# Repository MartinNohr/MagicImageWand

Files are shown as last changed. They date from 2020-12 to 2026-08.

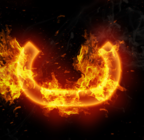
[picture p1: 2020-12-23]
ImageWandSampleImages/144/Fire-Alphabet/C.bmp

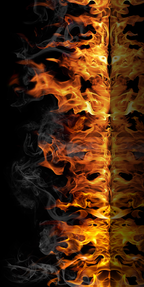
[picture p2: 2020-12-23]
ImageWandSampleImages/144/Fire/FlamesReflection3.bmp

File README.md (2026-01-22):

# MagicImageWand
Similar to the commercial PixelStick or MagiLight products, but designed for DIY.
This is a collaboration project with dirkessl (and possibly others) on a new and improved version of the LED Image Painter project.
It displays bmp files and built-in patterns in the air to be captured with time exposures.
The images are displayed using one or two 144 LED RGB pixel arrays.
The processor was originally the TTGO T-Display with the TFT display, the latest version uses the newer TTGO T-Display S3 chip. Software only support has also been added for the TTGO T4 with the larger display, but no 3D parts have been designed for that board.
It has a nice menu system and single rotary dial button for control.
This device can also be used as a simple light wand with color, saturation, and brightness controls.
It has optional exFat reading to support SD cards >32GB. This is enabled with a switch in the .h file, USE_STANDARD_SD, set to 0. 1 Uses the basic SD library.
<p>For exFat support this library must be included: https://github.com/greiman/SdFat
<br>The display is handled with this library: https://github.com/Bodmer/TFT_eSPI
<p>The file user_setup_select.h needs two lines modified.
<br>uncomment:
<br>#include &ltUser_Setups/Setup25_TTGO_T_Display.h&gt 
<br>comment:
<br>//#include &ltUser_Setup.h&gt

A more detailed setup Instruction for Arduino IDE is available in the Wiki https://github.com/MartinNohr/MagicImageWand/wiki/9.-Compiling-from-source
NOTE: TTGO Magic Image Wand Remote.pdf is used for a remote control camera shutter release designed by dirkessl. It is not part of the MIW project. Support for this concept will be added in the future. It will be possible then to have the MIW actually control the camera shutter.
  NOTE: The JSON library is no longer needed for this project, although it may come back someday! It was used by the bluetooth library for the Phone App. This was deprecated in favor of using a web server.

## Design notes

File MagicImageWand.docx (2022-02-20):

# Magic Image Wand

Using TTGO T1 (T-Display)

# 1 Introduction

## 1.1 History

This design was inspired but not copied from the PixelStick commercial product. I have not owned, used or even touched an official PixelStick, I haven’t even read their manual. I did briefly look at the marketing material on their website to get an idea of how it worked. I was also inspired by the light wand developed by photographer Michael Ross. I started out building one following Michael’s instructions. It used the Mega2560 Arduino and a 2-line display with some buttons. I started adding features and quickly ran out of memory. I also wanted to support a second 1-meter LED strip. At this point I decided to do a total rewrite and use the newer much faster esp32 modules. This let the feature list grow and the additionally the strip display speed was increased dramatically. The first version used an OLED display esp32 from Heltec. After that I discovered the TTGO with a color TFT display. After some more code re-writing and feature adding the TTGO version was created!

## 1.2 Version 2.26

This is the software version used for this documentation.

Changes to 2.26

- Added new scroll mode to the run screen. It now scrolls like the menus. There is a setting in the “Run Screen Settings” to enable the previous method of keeping the top line as the current file.
- Added help explanations for menu items using a long press on btn0. Only a few help texts have been added, more will be added in the future.

## 1.3 Using with Your Camera

Put your camera on a tripod and set it for a long enough time exposure so the shutter is open for at least the time it takes to display the image. Stand at your chosen starting position and open the camera shutter. Press the Image Painter start button and walk from right to left (looking at the camera), or left to right if you prefer, it is adjustable from the menus. Walk smoothly or erratically and hold the wand in the same position or wave it around. Use your creativity and see what kinds of images you can create.

## 1.4 Description

The Magic Image Wand consists of the following major parts. The parts are all connected together into a single unit. The optional second LED strip is easily removed or added so the system fits into a smaller space.

1. LED strip. This is an aluminum extrusion with 144 LEDs and a diffuser cover. The LEDs are available with an adhesive backing that is used to stick the strip inside the extrusion.
2. Fixed Handle. The rotary control button is on the handle which is used to hold the Image Painter. The button is under your thumb and can be pushed and rotated.
3. Rotating Handle. This is useful when two LED strips are attached. It allows the user to spin the light stick.
4. Control Unit. This box holds the ESP32 computer that runs the LED strips and reads the rotary button switch.
  a. TFT Display. The TTGO T1 ESP32 module used includes a small TFT display that is used to show the file selections. It is also used to show menus so that the various settings can be changed. It can even display a preview of the image file.
5. 18650 Batteries. These are the rechargeable batteries that run the control unit and the LED strips. They are held in the case underneath the handle.
6. ARCA tripod mount. This can be placed anywhere on the lower LED strip. It is used for holding the MIW on a tripod which is very useful when using it as a light source. The mount is also used to adjust the balance when using the spinner handle. It can be moved up or down until the balance point is at the spinner handle. This will make rotation much smoother.
7. There are two LED end caps that protect the end of the aluminum extrusions holding the LED strips.
8. Roller Encoder Wheel. This wheel is used to control the display speed while rolling on the ground. It will allow for very exact image timing. The good news is the software supports it but the bad news is that the hardware mount for the wheel has not been designed yet. The connection to this is labelled “frame sensor” on the PCB and schematic.

## 1.5 144 or 288 pixels

The Magic Image Wand uses one or two WS3812B pixel strips that have 144 pixels per meter. Each meter strip is made from two 72-pixel strips. This results in a slight gap in the middle that can be seen in some images. When the second strip is installed the power and data wires make it difficult to get the pixels close together. This results in a dark gap in the middle of the two strips that can be seen with some images. This problem can be avoided by running wires to the ends of the strips instead of the middle. There is an option in the settings to handle this.

The LED count can be set if strips other than 144 are desired.

## 1.6 Limitations

At full brightness, each strip uses 43 Watts when all the LEDs are lit. If full brightness is required then the voltage regulator must be able to supply enough current. However, some images do not have all of the LEDs lit at the same time so the brightness can sometimes be set to full power. For example, if the strip never has more than half of the LEDs on then the power consumption is only 21 Watts. In practice however I have found that due to the long night exposures it is seldom necessary to go brighter than about ¼ power.

## 1.7 Processing BMP Images

The images can be either 144 or 288 pixels in height. They must be rotated 90 degrees CCW and saved as 24bit color in Windows byte order. They can have as many pixels as desired for the width. The easiest way to build an image is to create the image as 144/288 pixels tall and as wide as needed. Remember that black will be transparent in the final image. Once the image looks good it can be rotated 90 degrees CCW and saved as a 24-bit bmp file. The bmp file is then saved to the micro-SD card.

There is a website that will convert images into the correct format.

https://www.essl.de/static/lighty/

# 2 Examples

I have posted some example photos on youtube.com and thingiverse.com. People more creative than me will create much more interesting images. I am including these just to illustrate a few simple examples. You can also go search the web for PixelStick images to get more inspiration.

Here are the links. The youtube links are for earlier versions.

https://www.youtube.com/watch?v=2L3TWKf_4T8

https://www.youtube.com/watch?v=_nibSs949mA

https://www.thingiverse.com/thing:4660045

https://www.thingiverse.com/thing:4613446

https://www.thingiverse.com/thing:4815316 the TTGO version

# 3 Button Operations

All operations can be controlled by the rotary push button on the handle, this makes the image painter usable with one hand. Read about btn0 and btn1 below. The display shows the options and settings and filenames. The dial can be rotated left or right to choose items. The button is clicked to select the current item. A long press is used to access other options and is done by holding the button down for about a ½ second or longer. This long press time is also adjustable if a longer or shorter time is preferred. The system has two modes of operation. After booting the display shows the currently selected file. Rotating the dial left and right will move through the files on the SD card, or the internal patterns if they have been selected. Clicking the button starts the LED strip display. At this point the user walks around with the wand or waves it around depending on what effect is desired. The display shows the progress of the file and how much time is remaining. Settings are available to control the display speed, repeating the file, or even automatically skipping to the next file. The image can even be played twice, first forward and then backward for a mirror like effect. There is a chain option that will play all of the files from the current selection to the final file in the current folder. The brightness of the LEDs are of course also adjustable to balance the lighting with the rest of the scene.

To adjust settings a long press is used on the dial or a simple press on btn1 which will open the last menu that was used. A long press while in the menus returns to the normal play mode. Each menu except the main menu has also at least one entry to return to the previous menu.

## 3.1 Dedicated Buttons – Button0(bn0) and Button1(btn1)

There are two dedicated buttons on the top left of the TTGO device. The top one is called btn0 and the bottom one is called btn1. Both these buttons support both clicking and long presses. A long press of both buttons will reboot the system The functions of these buttons depend on the current operating mode as described next. Common to all modes is that clicking btn1 will always emulate a long press of the dial button.

### 3.1.1 btn0/btn1 During Run Mode

btn0 will preview the current BMP file. This easier than navigating to the menu entry that does the image preview.

Long btn0 rotates the display through all four possible positions. If the display is upside down, the image file will also be rotated upside down. This is useful when using a single strip and holding it high in the air. A long press on the lower button turns on the lightbar feature. These actions can be modified in the system menu.

### 3.1.2 bnt0/btn1 During Menu Mode

btn0 returns to the previous menu. It does nothing if at the top menu. Long btn0 displays some help (if available) about the current menu item.

Long btn1 acts same as clicking the dial button.

### 3.1.3 btn0/btn1 During Integer Entry

btn0 cycles through the allowed increment values. Long btn0 resets the value to the original value. btn1 or dial click saves the new value and closes the number entry.

### 3.1.4 btn0/btn1 During Light Bar

btn0 cycles through the available increment values. Long btn0 increments the delay value which affects the auto cycle mode of the light bar. btn1 or dial click closes the light bar.

### 3.1.5 Btn0/btn1 During Image Preview

Btn0 or btn1 exits preview mode. A long press of btn0 or clicking the dial will show the image information screen. A long press of btn1 toggles the dial rotation mode. The first mode is that the dial scrolls the image preview left and right, this is useful for longer images. The other mode will move through the image files on the SD card. This is used as a visual way to select the current file. Rotating one way previews the next file and the other direction previews the previous file. Folders are ignored. Each long press of btn0 will cycle the starting offset of the image between the values of 0, 5, and 9. This allows the entire 144 pixels to be viewed on the 135 pixel display by changing the start offset.

## 3.2 File Control Settings

There are more details below in the section on menus but here is a quick list of the things that can be changed for controlling the image display.

1. LED brightness.
2. Color Balance. Set the white balance for special effects or to correct color casts.
3. Gamma Correction. Adjust the display to match closer to our color vision at different brightness levels.
4. Column time, how long each frame is displayed. Note that even when set to 0 there is a minimum time which is determined by the amount of time used to load the LED’s. See the menu section below for more details. Frame advance can also be set to manual so the frame only changes when the button is pressed, or the dial is rotated.
5. Fixed display time. It is also possible to have the system calculate the frame hold time. You just set how long in seconds you want the image to take and it will set the correct frame time based on the image size.
6. Reverse. This allows the user to walk from right to left or left to right.
7. Upside Down. This allows the user to hold the wand high in the air without modifying the image file.
8. Pixel Double. This uses two pixels for each one so a 144 pixel images can be displayed on the entire 288 pixels when two strips are installed.
9. Scaling. This will reduce a 288-pixel image to 144 pixels.
10. Mirror. Plays the file twice, first forward, and then in reverse.
11. Chain. Plays all the files from the current file to the last file in the current folder. Files are always in alphabetical order.
12. Start Delay. A wait after pressing the button until the file starts. All delays are specified in 1/10 seconds.
13. Repeat Count. How many times to repeat a file.
14. Repeat Delay. A wait in between file repeats.
15. Chain Repeat. How many times to repeat a chain.
16. Chain Delay. A pause in between chain repeats.
17. Built-In or File. Choose files from the SD or from a set of built-in patterns.
18. Change settings for various built-in patterns.
19. Select Folder. Choose a folder on the SD card to look for BMP files.
20. Display Settings. Control some menu operations and display options.
21. MIW. Manages files that change settings for folders and files. These setting files are loaded when a folder is selected or when a file is run. The settings for a file revert to the original values after running the file. These files are also text and can be edited if desired for special operations. The file version will apply the settings when the named file is displayed. The folder version is loaded when a folder is selected.
22. Saved Settings. Change the settings that can be optionally loaded at boot time. It is also possible to save the current settings and manually load them when needed.
23. Macros. There are ten macro slots (0 to 9) available. Each of these can either load all of the settings or run a recorded sequence of operations. The record command records the images as they are played and the same sequence can then be played again using the run command. The save command stores the current settings which can then be restored with the load command.
24. A dedicated button on the TTGO is used to preview the BMP file on the display.
25. The other dedicated button performs the same operation as a long press on the dial button.
26. Reboot. This will reset the system. It can of course also be done by unplugging the battery from the power supply or including a power switch for the power.

## 3.3 Rotating and Clicking Button

The handle button is rotated and clicked to select different files, menu items, and to change settings. In the menus, boolean values toggle with each click. Multiple selections cycle through all the available options. Integer values go to another screen that shows the minimum and maximum values. Rotating the dial right increases the value while rotating to the left decreases it by the increment amount. The increment amount can be changed by clicking the button which will cycle between different values. One of the values will be a reset to the original value, activated with a long press. A long press is also used to accept the new value and return to the menu. A * indicates the active menu line. A + in front of the menu means another menu will be activated. The “Return…” menu goes back to the previous menu when clicked. A long press will return to file select/run mode. The current menu entry is remembered so that it will return to the same place when the long press is done from the select/run screen.

In select/run mode the current file is displayed on the top line. Optionally the next three files will be displayed below. Rotating the dial right moves the next file to the top line and rotating left moves the previous file back. By default it will stop at the first and the last file. An option allows rollover, so going left from the first file moves to the last file and moving right at the last file will display the first file again. This option also causes menus to behave similarly.

When a file is running after clicking the button the top of the display will show the progress of the file. The current filename is displayed. The line under the file will show the remaining seconds for the file. The rest of the screen will show the various delays, repeats, and chain information when those options are activated.

### 3.3.1 Button Menu Operations

Left/ Right

Select menu

Select file

Inc/ Dec integers

Long press

Open menu system, goes to the remembered menu point

Return to run mode, the current menu point is remembered

Accept integer

Click

Run file when in run mode

Select menu item, including return to previous menu

Toggle booleans

Rotate through multiple selections

# 4 Menus

There are two menu set, full and simple. The full one contains all of the options and can be somewhat time consuming to navigate during normal use. The simple menu has the most used options and is very short.

All menus except the main one have the first line indicating what menu this is. There is a ‘-‘ in front that indicates clicking on this menu will go back to the previous menu. Submenus also have the last entry as “-Back” which will return to the previous menu.

# 5 Simple Menu Details

## 5.1 Menu: Simple

This is a toggle between the full and simple menus. It names the current one in case it isn’t obvious! Just click on it to change to the other one. The setting will be remembered across rebooting.

## 5.2 Images: SD Card BMP | Built-In

This will show which images are currently available, the built-in ones or the SD card BMP files.

## 5.3 Column Time: 10 mS

This displays the current frame time and can be used to adjust the time. It can adjusted from 0 to 500 mS.

## 5.4 Brightness: 30/255

This sets and adjusts the LED strip brightness. 255 is full brightness.

## 5.5 Run Macro: #(0-9)

This will start running the selected macro number, from #0 to #9.

## 5.6 Select Macro: #(0-9)

This command will list all 10 macro names with an indicator if it is available or not. Clicking on one will make that the current macro for the run command.

## 5.7 Sleep

This menu entry makes the MIW enter sleep mode, which uses little power. Pressing any key will wake the system up with the same settings it had before.

# 6 Full Menu Details

Following is a detailed list of all the menu entries and what they do. Menu items that open another menu (a submenu) start with a ‘+’. Most submenus also have a first and last menu entry that returns to the menu above. Depending on the “menu choice” setting found in the menu settings of the system menu, either an ‘*’ is shown in front of the active menu line or the menu line is highlighted. The top menu will have a small white triangle indicating that there are menu items that are not visible due to scrolling. Just keep rotating the knob to the left and they will appear. Similarly the last entry on the screen will have a small white triangle if there are more menu items below. Scroll right to make them visible as the ‘*’ or highlight indicator moves down.

The submenu details are also described below after each menu item. Submenus have a ‘+’ at the start.

Some menu items may change depending on other selections. For example, chain options are not displayed unless chaining is enabled.

## 6.1 Menu: Full

Select this to toggle between the simple and full menu systems.

## 6.2 Images: SD Card BMP | Built-In

Clicking this selection will toggle between running files from the SD card or using the built-in patterns.

## 6.3 Preview BMP

This will display the currently selected BMP file on the screen. Note that the upper dedicated button (button 0) does the same operation. This menu item appears only when CD Card is selected. Since the images are 144 pixels and the display is only 135, 9 pixels total are trimmed from top and bottom of the image. The starting offset in the preview menu sets how many pixels are ignored at the top. Long press btn0 can be used to change this value while previewing. Each long press of btn0 cycles through the values of 0, 5, and 9 pixels. The image can be scrolled left and right using the dial if the image is longer than 240 columns. The sideways scroll amount defaults to 120 pixels, but the amount can be set in the system menu display settings menu A single click toggles between the image preview and a screen showing the width and height of the image. Pressing the upper preview button, or a long press on the dial, or the lower dedicated button exits the preview display.

The image preview has two modes for using the rotating dial. The default mode is to scroll the iamge sideways when possible. The other mode will scroll through the image files. This is a visual way to select the current file. The modes are toggled by a long press of btn1.

Clicking the dial button while previewing a file will display a screen with the size of the image in pixels, the length that should be walked for the correct aspect ratio, and how long the image will be displayed at the current column hold time.

There is a dedicated button on the top left that can also be used to preview the file. Pressing it again will return to the previous menu or file selection.

If the images are designed for the second LED strip then the images can be 288 pixels high. The preview function will then ignore every other pixel so the preview will fit in the display.

The preview can also be set to automatically scroll if it is long enough. The speed and amount of pixels to jump in this auto scroll mode are adjustable from the preview settings menu found in the system menu.

## 6.4 +Image Settings

This submenu has the settings that control display attributes of the image files. The frame hold time is also used by some of the built-in image functions.

### 6.4.1 Timing Type: Column | Image

This is a Boolean that switches between using a set frame hold time for each column of the image file or a calculated time based on the desired total display time. It is sometimes more convenient to set the total time that the image file is displayed. This mode will automatically calculate the frame hold time such that the image will display for the chosen time. It is possible to request a time that is too fast for the image painter. If the calculated frame hold is less than about 4 mS the software cannot read the SD card fast enough to keep up. The image painter will do the best it can, and the actual time will be displayed on the screen as the image plays.

### 6.4.2 Column Time: 10mS

This selection shows and allows to be changed, the time in mSecs (see note below) that each line of information from the BMP file is displayed on the LED strip. It is commonly used to adjust the walking time while the file is being displayed. It is only applicable when Frame Advance is set to auto. The valid range is 0 to 500 mS.

Note: This time is actually added to the minimum time that it takes to update the LED’s in the strip. Each bit of information takes 1.2 uS and each LED needs 24 bits. If there are 144 LED’s then the total time to load the data is 1.2 uS x 24 x 144 = 4.32 mS. There is also a reset time at the end that loads the data into the LED’s of >50 uS. Some brands require up to 1 mS so it is safest to assume that the column update time is about 5 mS. This time is added to the time set in the frame hold value, I.E. a hold value of 0 will still have a 5 mS frame time. There might also be additional time required for reading slower SD cards. Also be aware that displaying the file in reverse will slow down due to reading the SD file in the reverse order. A 900 column image would in theory take about 3.9 S. In testing we have found that reading the SD card actually slows this down to about 6 Seconds. Work is being done to try and improve this.

### 6.4.3 Image Time: 5 S

When image time is selected as described above in Column Time this menu item allows the time to be set in seconds that the image will be displayed. The necessary column time will be calculated and used while displaying the image file. This value will not be saved in the column time so if column time is selected again it will show the original value.

### 6.4.4 Start Delay: 0.0 S

This value delays the image display after the start button is pressed. It can be set in 1/10 second increments.

### 6.4.5 Fade I/O Columns: 0

This value is the number of columns (aka frames) that will be used for fading in and out during the display of an image file. It does not apply to the built-in patterns. For example, setting it to 20 will mean that the first 20 frames will start at a brightness of 0 and increase to the specified LED brightness. The last 20 frames will fade down to 0 on the last frame. This gives a softness to the starting and ending sides of the image. An option to have separate values for starting and ending has been considered but has not been implemented yet.

### 6.4.6 Upside Down: Yes | No

When set, the image pixels will be reversed. This allows the LED bar to be held upside down without making the image upside down. Note that a long press on button 0 will also toggle this.

### 6.4.7 Running Dial: None | Brightness | Speed

This menu controls what the dial does during image display. The brightness or speed (column display time) can be changed during display by rotating the dial. This can be used to create more interesting image effects by rotating the dial while walking.

### 6.4.8 Walk: Right-Left | Left-Right

This option changes the direction that the file is read for display. This allows the image to play forward or reverse. This allows the user to walk in the other direction or to simply reverse the image from left to right. The default is right to left, looking back at the camera. Right to left is usually best when recording a sequence of images into a macro. The images will then play back in the same order. If left to right is chosen, then the images recorded will play back in the reverse order. This is particularly important when spelling words with the individual letter image files during macro recording.

### 6.4.9 Play Mirror Image: No | Yes

This plays the image twice, once forward and then in reverse. This creates a mirror like effect.

### 6.4.10 Mirror Delay: 0.0 S

This is the delay before starting the mirror image display after the normal display is finished. I is used to create black space between the two parts of the image.

### 6.4.11 Scale Height to Fit: No | Yes

If the image is taller than 144/288 this option will ignore some pixels so that only 144/288 are displayed. It does not do any fancy scaling like Photoshop by looking at adjacent pixels, it simply ignores half of them so the image will fit.

### 6.4.12 144 to 288 Pixels: No | Yes (only when 288 pixels is set)

This doubles every pixel so a 144-pixel image will fill all 288 pixels. Of course, there isn’t any increase in resolution, but it does fill two strips if you don’t have a 288-pixel image.

### 6.4.13 Frame Advance: Auto | Step

In auto mode the frame hold time is used. In step mode each line is displayed until the button is pressed, the dial is rotated, or the frame (aka wheel) pulse counter closes the contact. If the frame pulse counter is zero then the dial is used to advance frames. Rotating to the right or clicking will display the next frame from the file. Rotating to the left will display the previous frame. This enables some creative uses of image by rotating the wheel left and right. Note that the mechanical wheel pulse counter has not been designed yet.

### 6.4.14 Frame Counter: 0

This value is the number of wheel pulses that will advance to the next frame when manual frame advance is set. Note that this option is set to a non-zero number it disables using the rotary dial to advance frames.

## 6.5 +Repeat/Chain Settings

This submenu contains settings that are used to repeat and chain images. Except for the chaining option it also applies to built-in images.

### 6.5.1 Repeat Count: 1

This is the number of times to repeat an image.

### 6.5.2 Repeat Delay: 0.0

When repeat count is greater than one this value will cause a delay before the image starts again. It is set in 1/10’s seconds.

### 6.5.3 Chain Files: Off | On

When this option is on all the files from the current one to the end of the last file in the current folder will be displayed. Since filenames are always sorted alphabetically this option will show a sorted list of files. If some other order is desired it is also possible to use the macro command to record the file order for display.

### 6.5.4 Chain Repeats: 1 (only when chain files on)

The entire chain will be repeated this many times.

### 6.5.5 Chain Delay: 0.0 (only when chain files on)

This time value is applied before starting each chain repeat after the first one.

### 6.5.6 Chain Wait Key: No | Yes (only when chain files on)

This is a Boolean setting that when true will wait for a key click or rotation after each file is displayed. You can then decide when to start showing the next file in the chain.

## 6.6 +LED Strip Settings

This submenu has settings for the LED strip.

### 6.6.1 Max Brightness: 25/255

This is the brightness from 1 to 255. Values above about 45 should not be used with the light bar unless the power supply can supply sufficient current. 255 white will use almost 7 amps! The version of the PCB with the onboard power supply can only supply 1.5A continuous. More than that will cause overheating and eventual destruction. High brightness values can be used for shorter image displays of course if there is some cool down time. A minute is usually sufficient for this. In practice it has been found that a brightness level of 15 to 25 is more than adequate for night photography. 7A would likely only be needed in a light bar used for studio lighting.

### 6.6.2 LED Controllers: 1 | 2

This is set to “1” or “2” depending on whether you have the second strip installed. There is not any method to detect a strip connected to the second control lines so it must be manually selected. When this value is changed a reboot is necessary because the fastled LED library does not handle runtime changes very well.

### 6.6.3 Total LEDs: 144 | (up to maximum value) 512

This is a number specifying how many total LED’s are available. It can be set from 1 to 512. For example, if there are two 144 LED strips, then this should be set to 288.

### 6.6.4 LED Wiring Mode: Middle | Serial | Outside

This option allows the wiring to the LED strips to be arranged in different ways to optimize the wand. Putting both LED inputs in the middle of the wand means shorter wires that do not have to extend to each end of the wand, but there will be a larger gap in the middle between the two strips since it is difficult to get the LED strips close with the power connecters there. Putting the bottom strip input on the bottom and connecting the output of the bottom to the input of the top LED allows for only one control wire but there will still be a black stripe in the middle due to the spacing needed for the wires. This is same problem as the first wiring situation. If the top strip has the data input at the top, then the gap in the middle can be eliminated. Make sure no electrical contact happens in the middle between the two LED strips. This approach does mean that it is necessary to run wires out to both ends of the wand, but in return there is no black stripe in the middle when using the wand.

- Middle - Both strips have data input in the middle.
- Serial - Bottom strip is fed data from the bottom and the middle has a connection through to the upper strip. This uses a single contoller while the others can use one or two controllers.
- Outside - The top strip is reversed and there is no connection between the strips in the middle. Both strips require long wires to the outer data feed locations.

### 6.6.5 Gamma Correction: On | Off

This option modifies the displayed colors at different brightness levels to more closely match our eyes color perception.

### 6.6.6 White Balance R: 255

This manually sets the strip Red brightness Values range from 0 to 255.

### 6.6.7 White Balance G: 255

This manually sets the strip Green brightness.

### 6.6.8 White Balance B: 255

This manually sets the strip Blue brightness.

### 6.6.9 Show White Balance

Selecting this displays the before and after result of setting the RGB levels. It runs for about 5 seconds.

## 6.7 +Various Built-In Settings

When built-ins are selected and the selected one has adjustable options the menu will appear here. More documentation may be added here later.

## 6.8 +MIW File Operations

MIW files are files that can load settings and display images. They are text and can be modified by using any text editor on them. The extension is always MIW (Magic Image Wand). There are menu items to create, run and delete them. Depending on the name some of them are automatically run under certain conditions as documented below.

MIW files only control the settings for files, none of the built-in image settings are saved in these files.

### 6.8.1 Save start.miw

This creates a file with the current settings. It is run whenever a folder is opened.

### 6.8.2 Load start.miw

This will manually run the file in the current folder.

### 6.8.3 Erase start.miw

This does just what it says: removes the start.miw file from the current folder.

### 6.8.4 +Associated Files

These are command files just like the start.miw file above, but they have the same name as a BMP file, but with the .miw extension of course. The file is run when a BMP file is started for display. This allows specific settings to always be applied to a specified BMP file.

#### 6.8.4.1 Save <filename>.miw

This saves the current settings for the currently selected BMP file.

#### 6.8.4.2 Load <filename>.miw

This loads the settings for the currently selected BMP file. It can be used to verify that the settings are in fact correct.

#### 6.8.4.3 Erase <filename>.miw

This command deletes the file associated the currently selected BMP file.

## 6.9 +Macros

Macro files are a powerful feature that can be used to record and run a set of images. There are 10 macro files allowed. They are named from 0.miw to 9.miw on the SD card in the root folder. They can also be edited on a computer by using a text editor if necessary. The easiest way to create one is to use the record menu entry as shown below.

Descriptive names can be assigned as described in the information section below.

### 6.9.1 Select Macro: #(0-9)

This selects the current macro number. It shows a list of all the macros along with information on whether it already exists or not. The user assigned name will be shown after the number. If no name has been assigned the name will show as either “Used” or “Empty”. Clicking on a line makes that macro # the active current macro # which is used by most of the following menu entries.

### 6.9.2 Run Macro: #(0-9)

This will run the currently selected macro number.

### 6.9.3 Override Settings: Off | On

This is used to override the image setttings that are stored in the macro file with each BMP file. An example using it would be if it was recorded with frame hold time that needs to be changed to a different value. Setting this to on will then use the current frame time instead of the one saved in the macro file.

### 6.9.4 Record Macro: Off | On

When set to on, the settings and displayed images will be appended to the currently selected macro number. It should be turned off when all the actions have been recorded. Use the delete command first if a sequence is to be recorded without appending.

### 6.9.5 Repeat Count: 1

This value repeats the macro run.

### 6.9.6 Repeat Delay: 0.0 S

This is the delay between each run of the macro when repeat is on.

### 6.9.7 Information: #(0-9)

This will display some information about the currently selected macro.

- The macro name, “Empty”, “Used”, or a manually entered description
- Number of BMP files
- The total time for display
- The total number of horizontal pixels
- The total distance to walk to maintain the correct aspect ration

A long press exits the display.

Rotating the dial will show the list of all the BMP files in the macro. Rotating the dial again left or right will scroll through the list if it is longer than 7 files.

Clicking button 0 (top left on the TTGO) allows entry of the descriptive text for the current macro. A long press exits and saves the text. There is help on the screen for other button operations. The screen shows a list of available letters, numbers, and other symptoms. Rotating the dial selects a character and clicking the dial appends it to the end of the text. A long press on button 1 (bottom left on the TTGO) toggles between upper and lower case letters.

### 6.9.8 Load: #(0-9)

This loads the settings in a macro file without running any image files contained in the file. If there are multiple settings the last one will be used.

### 6.9.9 Save: #(0-9)

This saves the current settings in a macro file without saving any image files to run.

### 6.9.10 Delete: #(0-9)

This erases the currently selected macro file. It is useful when a new sequence is to be recorded since the record action always appends new actions to the macro file.

### 6.9.11 Delete: Macro JSON File

This is a file on the SD card that contains information about each macro. If it gets corrupted or something seems wrong just delete this file. It will automatically be recreated when the system boots. The times, sizes, and files are obtained from the macro files. The description text is contained only in the JSON file so it will be lost and must be entered again from the information menu.

## 6.10 +Saved Settings

These settings are stored in the NVRAM section of the ESP32 and it is a useful way to set the defaults during boot time. The system settings are always automatically saved and loaded on startup. This means that LED strip, menu, and dial settings are effectively permanent, they will be saved and loaded automatically. Other settings can be loaded automatically by enabling the autoload switch.

There is a version number saved that will be compared when loading. A mismatch will force all settings to their default values. No message is displayed when this occurs.

### 6.10.1 Autoload Saved

This flag causes the EEPROM (NVRAM) values to be loaded at boot time. If off, then the factory settings will be loaded instead. If factory settings are desired the button should be pressed during booting. This will ignore the setting of this flag.

### 6.10.2 Save Current Settings

This saves the current settings. Built-in options settings are also saved. Note that MIW files do note save any of the built-in settings.

### 6.10.3 Load Saved Settings

This manually loads the settings from EEPROM.

### 6.10.4 Reset All Settings

This will reset everything to the factory values and erase the stored values in NVRAM.

### 6.10.5 Format EEPROM

This clears the NVRAM and formats it for storing the values.

## 6.11 +System Settings

Various system settings can be changed from this submenu. All these settings are automatically saved and are loaded automatically at boot time.

### 6.11.1 +Display Settings

#### 6.11.1.1 Display Rotation: 0 | 90 | 180 | 270

This rotates the display through the 4 positions so that it is readable when the wand is help upside down or sideways. This is particularly useful when using one LED strip and the wand should be held higher in the air. It is used in conjunction with setting the image also upside down. Using a long press on button 0 is the easiest way to do this since it adjusts both the image and the display upside down (for 180 only) at the same time.

#### 6.11.1.2 Dimming Mode: None | Timer | Sensor

This is used to set the dimming mode for the display. When set to None the display will always have the bright setting. The Timer setting will dim the display to the dim value after the specified number of seconds, any button action will restore the display brightness to the bright value. The Sensor option uses the light sensor to adjust the brightness between the bright and dim values.

The MIW will detect the presence of the light sensor during system initialization. If the sensor is not found it will not be selectable as a dimming mode. Note that this detection depends on some light hitting the sensor when first initialized. This means the MIW must not be factory reset in total darkness!

Some of the menu options will only appear for the mode setting where they are applicable.

#### 6.11.1.3 Bright Value: 50%

This is the TFT display brightness from 1 to 100%. It is often desirable to lower it when working in darkness.

#### 6.11.1.4 Display Dim Time: 0 S

When no buttons or dial rotations happen for this amount of time the display will dim to preserve power.

#### 6.11.1.5 Dim Value: 30%

This is the value the display will dim to when the dim timer expires. This menu item is hidden when the dim time value is 0.

#### 6.11.1.6 +Light Sensor

The settings in this menu will control how the display is controlled by the ambient light.

##### 6.11.1.6.1 Read Light Sensor

This will continuously display the sensor value so that appropriate numbers can be chosen for the Dim and Bright value settings. Less light gives higher values, and more light gives lower values. A normal illuminated room should show 0 or very close to it. Remember that the MIW is designed to be used in dim lighting at night. Very low light can easily give a number over 4000. The display brightness will be adjusted depending on the sensor light reading between the Dim and Bright values.

##### 6.11.1.6.2 Dim Value: number

This number is set to the value read in the lowest ambient light that is expected.

##### 6.11.1.6.3 Bright Value: number

This number is set to the value read for the brightest ambient light expected.

#### 6.11.1.7 Sideways Scroll Settings

When lines are too long for the display, they will scroll sideways so the entire line can be seen. The speeds can be adjusted using the following menu items.

##### 6.11.1.7.1 Sideways Scroll Speed: 25 mS

This is how fast the line scrolls to the left. Smaller numbers are faster, since it is actually the pause time per pixel.

##### 6.11.1.7.2 Sideways Scroll Pause: 20

This is the number of scroll speed times to wait at the end of each line before switching direction and scrolling again. For example, when the scroll speed is 25 mS and the pause is 20 the scrolling will pause for 25 x 20 = 500 mS at end of the scrolling.

##### 6.11.1.7.3 Sideways Scroll Reverse: 3x

This is a speed multiplier, well actually a divider of the time, that controls the reverse scroll speed. 3x means it will scroll three times faster in reverse than it does going forward.

#### 6.11.1.8 Menu Choice: Color | *

This controls the indicator on menus for the current selection. Color means that the background and foreground colors are reversed. The ‘*’ choice leaves the text colors the same and adds a ‘*’ to the beginning of the active menu line.

#### 6.11.1.9 Text Color

This sets the text color to various allowed values. The default is blue.

#### 6.11.1.10 Menu Wrap: No | Yes

When this is off scrolling of both files and menu items is pinned at the top and bottom of the list. If wrap is on, then rotation the dial to the right when at the last entry will go to the first entry and rotation left from the first entry to move to the last entry.

### 6.11.2 +Run Screen Settings

#### 6.11.2.1 Show BMP on LCD: No | Yes

This option displays the bmp on the display along with the LED display. As each column is displayed on the LED strip the same column will be displayed on the TFT screen. This gives you some visual feedback as the image is processed. When off the %, progress bar and other values like repeats will be displayed.

#### 6.11.2.2 Current File: Color | Normal

This controls the display of the top line in wand run mode, which displays the current image file or the current built-in pattern. There are two choices.

- Color, displays the name in black letters with color background
- Normal, displays the name in color with black background

#### 6.11.2.3 Show More Files: Yes | No

In run mode the top line always shows the file to be displayed. When this flag is on the following lines on the display will show the next few files in the current folder.

#### 6.11.2.4 File on Top Line: No | Yes

When “Yes” the run screen shows the current file on the top line always. When “No” the cursor will move down and up just like it does during menu display.

#### 6.11.2.5 Show Folder: Yes | No

The top line in run mode shows the current file to be run. If this flag is on it will include the folder path. It should be turned off if the folder path is too long.

#### 6.11.2.6 Progress Bar: On | Off

When a file is running the second line of the TFT display can show a progress bar. This option is used to turn it on or off.

### 6.11.3 +Dial & Button Settings

#### 6.11.3.1 Dial: Normal | Reverse

This sets the direction of the dial that moves forward or backward through choices.

#### 6.11.3.2 Pulse Count: 1-5

It is sometimes desirable to reduce the sensitivity of the dial to rotation. Wearing gloves or shivering fingers is an example. This allows a counter to be set such that more than one click detent will be required to produce a dial motion. For example, setting this to 2 means that the dial must be moved two clicks before it would change the selection. Values from 1 to 5 are valid. This value works in conjunction with the pulse timer.

#### 6.11.3.3 Pulse Timer: 500 mS

This is the amount of time that rotary pulses must follow to be counted. For example, if the pulse count is set to 2 then two pulses (dial clicks) must be within this amount of time in order to be counted as a dial pulse rotation. After a click, if the next click (pulse) is later than this time it will be ignored. This is designed to reduce the sensitivity of the dial. This can be useful when it is cold, and the hands are shaking!

#### 6.11.3.4 Long Press Counts: 40

This value determines how long a long press is. Bigger numbers mean the button must be held down longer to be considered a long press.

#### 6.11.3.5 Btn0 Long: DisplayRotation | LightBar

This is the action for a long press on the top left button. UpsideDown rotates the display and also shows the BMP reversed. LightBar runs the light bar function to use the wand as a light source. There will probably be more choices in the future.

#### 6.11.3.6 Btn1 Long: LightBar | DisplayRotation

This is the action for a long press on the bottom left button. There will probably be more choices in the future.

#### 6.11.3.7 Rotate Dial Type: Toggle | Pulse

There are two types (maybe more) of rotary dial encoding methods. Some pulse the A and B lines for each click of rotation while other just change to other state. The first kind always leaves A and B open and simply pulse A and B closed for a short period of time with each rotation click. This one is called “pulse”. The other kind changes between open and closed with each click. This is called “toggle”. The time relationship between the A and B contact closures determines the direction of rotation.

After a system reset to factory or the first time a new version of the software is loaded the software will try to determine which kind of rotary switch exists. If the rotary switch is the toggle kind, it might ask for the dial to be rotated one click in either direction. This happens when the dial is in the contacts open position since this is the normal position for the pulse dial type and the software can’t determine what the switch type is. Because the automatic detection works perfectly this menu option will rarely be needed.

If this option is set incorrectly the following symptoms will be noticed:

      1. Each rotation click will move by two positions.
      2. It takes two rotation clicks to move one position.

If the system has either of these symptoms, then try the other option. Alternatively use the reset to factory and let the automatic switch detection fix it.

### 6.11.4 +Preview Settings

#### 6.11.4.1 Scroll Mode: Sideways

This stores the preview option for the dial scrolling sideways or browsing the files on the SD card. It can be toggled here or during preview with a long press of btn1, the lower left button.

#### 6.11.4.2 Top Start Offset: 5 px

This sets the starting point for the top of the image display. Because most images are 144 and the display is only 135 pixels it is not possible to display all of the image height. The default value of 5 will remove the top 5 pixels on the preview display. This will result in 4 more pixels missing on the bottom of the image. The value can be set from 0 to 10 as desired.

#### 6.11.4.3 Dial Scroll Pixels: 120 px

This is the number of pixel columns that the preview display of an image is scrolled with each increment of the rotary dial. The default value is half the screen width.

#### 6.11.4.4 Auto Scroll Time: 0 mS

This is used to cause the preview to automatically scroll. The value is in mSeconds but due to the speed of reading the SD card and the display, values below 100 are about the same. The display resets to the beginning after it reaches the end.

#### 6.11.4.5 Auto Scroll Pixels: 1 px

This is the number of pixels to scroll when auto scroll is enabled.

### 6.11.5 Sleep Time: 0 Min

If this is set to a non-zero value, the MIW will go to sleep mode if nothing is run or selected for that many minutes.

### 6.11.6 +Battery Settings

This menu has all the battery related settings.

Battery Calibration: The PCB is built with 10% tolerance components and battery voltages will differ slightly from different vendors. Because of this the most accurate battery charge indication will only be obtained after calibrating the high (100%) and low (0%) settings. The “Show Battery” menu entry is used to read the current battery level. For two cells this number will typically be in the 1000 to 1800 range.

Note that there are two main version of the PCB. One has an on-board power supply while the other requires an external power supply. The battery sensing line is separate for the latter one.

Quick Battery Calibration

- Fully charge the batteries
- Use “Show Battery” menu to obtain the high value number
- Put this number in “100% Battery”
- Multiple this number by 0.71 and put in “0% Battery”

More Accurate 0% Battery Calibration

For the most accurate 0% battery setting it will be necessary to use an adjustable voltage supply connected to the battery sense line (or the battery supply line on the on-board PCB). Set this voltage to 5.8 before connecting the power supply. You can also try lower voltages until the power supply (voltage regulator) does not supply 5V anymore. Do not go below 5.5V for two cells because a cell should never go below 2.75V. Next use “Read Battery” to obtain the value for the 0% setting.

#### 6.11.6.1 Low Battery Sleep: Yes | No

When this is set to “Yes” the MIW will go to sleep when the current battery level value is below the 0% setting. The MIW will not turn on until the batteries are replaced or recharged.

#### 6.11.6.2 Show Battery: Yes | No

This setting controls the display of the battery level on the main screen. When on it will use the bottom line to right of the display. It shows both a graphic value and text of the % value.

#### 6.11.6.3 Read Battery

This will display the current value of the battery sense line on the PCB. It is useful to calibrate your batteries as described in the “Battery Settings” section above.

#### 6.11.6.4 100% Battery: high number

This is the full battery value. It should be set to the value from “Read Battery” obtained with fully charged batteries.

#### 6.11.6.5 0% Battery: low number

This is the lowest acceptable battery value. It is approximately 0.71 times the full value. LiIon batteries should never be discharged below 2.75 volts (5.5 v for two batteries), but the actual value may depend on the power supply used, which is often around 5.8 volts.

#### 6.11.6.6 Battery Count: 1-4

This is set to the number of cells and will load default values for 100% and 0%. If set to 1, the power supply must of course be a boost regulator. Cells from 2 to 4 assume a buck regulator which lowers the output voltage to 5V.

### 6.11.7 IP: 192.168.4.1

This is the address of the web page server built into the wand. It is very experimental and not complete yet. The only useful function is the ability to upload or download image files directly to the wand from a web browser on a phone or computer without removing the micro-SD card. More features will be added in the future, including complete control of the wand. To use it, first connect to the MIW….. network. The password is 12345678. Then point the browser to the IP address.

### 6.11.8 Reset All Settings

This resets all the values to factory settings.

## 6.12 Light Bar

This selection turns the Image Wand into an adjustable LED light source. All the LEDs are turned on. The menu can then be used to change the Hue, saturation, and brightness levels. The number of LEDs that are lit can also be changed, along with starting at the end or the middle. The maximum brightness is limited by the strip brightness that is set in the strip menu.

The default allows setting the brightness, hue and saturation, but it can also be changed to use RGB values or Kelvin. The default increment unit is 10 for each click of the dial but that can be adjusted for finer resolution.

Btn0 is used to cycle the increment that the dial uses. The values are 1, 10, 100, 256. Pressing Btn0 selects the next choice.

A long press of Btn0 and Btn1 will increment or decrement the current delay value by the increment value. The delay value is in mSec and is used to slow down the stepping when the dial is rotated. For example: if the increment is set to 10 and the dial is rotated right one click with the current Hue of 5, the hue will step from 5 to 15 with the delay after each step. This can provide a smooth change of the Hue value over a time value determined by the increment times the delay. All of the other settings behave the same as Hue. Experiment to see how they work!

A long press is used to turn the light bar off again.

## 6.13 +Light Bar Settings

This is a menu that sets the default values for the light bar option.

### 6.13.1 Allow Rollover

Allows values to rollover as the dial is rotated instead of stopping at the min and max.

### 6.13.2 Color Mode: HSV | RGB | Kelvin

HSL or RBG or Kelvin can be chosen. The choice will affect some of the following menu lines.

### 6.13.3 Hue: 0

Adjusts this value.

### 6.13.4 Saturation: 255

Adjusts this value. 0 is no color.

### 6.13.5 Brightness: 255

Adjusts this value. It is relative to the maximum set in the system LED menu.

### 6.13.6 Red: 255

Allows the red value to be adjusted.

### 6.13.7 Green: 255

Allows the green value to be adjusted.

### 6.13.8 Blue: 255

Allows the blue value to be adjusted.

### 6.13.9 Pixels: 288

How many pixels to be displayed. It is from 1 to the total number of LED pixels.

### 6.13.10 Temp: Candle 1900K

Various Kelvin equivalent choices are available.

### 6.13.11 From: Middle | End

There are two choices, Middle, and End. This selects where lit LED pixels start when the above pixel value is less than the full strip length. The end can be changed using the LED strip reverse setting described earlier.

## 6.14 Reboot

This resets the system. Pressing btn0 and btn1 for a long press time will do the same.

## 6.15 Sleep

This puts the TTGO into a low power mode. Pressing the button will wake it up again. It is useful to save the battery while not losing any of the current settings. Alternatively the settings can be saved and then restored after rebooting the wand.

# 7 Built-In Patterns

There are several built-in pattern generators. Some of them have settings that can be adjusted from the entry that appears on the first menu when a particular built-in is selected. The available built-ins are listed below.

## 7.1 Barber Pole

This creates a rolling red, white, and blue pattern. It will create diagonal patterns. The speed is controllable by setting the frame hold time.

## 7.2 Beats

Colored bars moving up and down.

## 7.3 Bouncy Balls

This uses physics calculations to simulate some colored bouncing balls. The number of balls can be set up to 8, each will have its own color. The speed can be changed using the same built-in menu. The frame hold time is not used. On an image it makes some interesting decaying inverted second order polynomial traces. Sorry about the math terms! Play with it.

## 7.4 Checker Board

Alternating black and white boxes. The speed is adjustable using the built-in menu or the frame hold time.

## 7.5 Confetti

Interesting color dots that appear and then fade out.

## 7.6 Cylon Eye

This was inspired from the BattleStar Galactica movies, the evil Cylon eyes.

## 7.7 Juggle

This shows some color bars that move up and down and cross over each other.

## 7.8 Lines

This produces a series of stripes.

## 7.9 Meteor

This looks kind of like a meteor moving from one end of the strip to the other.

## 7.10 One Dot

Actually, this is four dots, red, green, blue and white. They move one at a time from one end to the other. It is probably mostly useful for testing the wand. That’s why it was written originally.

## 7.11 Rainbow

The color, number of repeats, and color cycling can be controlled. It is even possible to add random sparkles to add a bit more interest. Try moving the wand in an arc for interesting rainbow-like patterns.

## 7.12 Rainbow Pulse

This is rainbow that starts from the bottom, sweeps up, and then back down again until it is gone.

## 7.13 Random Bars

This produces solid colors that alternate randomly. An option sets black in between each color bar. Waving the wand can make some interesting patterns in the air.

## 7.14 Sine Trails

A little more math here traces a color blob using the sine function.

## 7.15 Solid Color

This is probably one of the more useful patterns. It allows the LED strip to be used as a light source. The color can be controlled with the dial as well as the saturation and brightness. A setting allows the RGB values to be entered if that is desired. The brightness value is limited by the LED strip brightness setting from the main LED settings menu. So if more brightness is needed that value must be changed. The LED strip will stay on until a long press turns it off.

## 7.16 Twinkle

A display of dots of various colors that change color randomly.

## 7.17 Two Dots

This is like the One Dot, except that two dots are on the strip. They start at opposite ends and cross over in the middle. It was also written originally to test the code and the LED strip.

## 7.18 Wedge

Creates a triangle type pattern.

# 8 Menu structure

Here is a chart of the menus. Note that menus that are not applicable will not be displayed. For example, choosing Frame Time means that Fixed Time will not appear in the menu while choosing Fixed Time means that Frame Hold won’t appear. Some submenus are not shown in order to keep this chart smaller. One menu missing is the battery one.
Image Settings
Repeat/Chain Settings
Timing Type
Column Time
Image Time
Repeat Count
Chain Files
Chain Repeats
Start Delay
Upside Down
Walk
Play Mirror Image
Scale Height to Fit
Repeat Delay
LED Strip Settings
Brightness
Max Current
Gamma Correction
Full Menu
Save start.miw
Load start.miw
Erase start.miw
Associated Files
Macros
Select Macro #(0-9)
Run
Repeat Count
Repeat Delay
Save
Delete
Saved Settings
Autoload Saved
Save Current Settings
Load Saved Settings
System Settings
Bright Value
Menu Wrap
LIght Bar
Reboot
Fade I/O Columns
Frame Advance
Frame Counter
144 to 288 Pixels
Chain Delay
RED
GREEN
BLUE
Show White Balance
Record
Load
Text Color
Sleep
Chain Wait Key
Light Bar Settings
LED Controllers
Total LEDs
LED Wiring
MIW File Operations
Running Dial
Override Settings
Reset All Settings
Format EEPROM
Display Settings
Display Rotation
Display Dim Time
Light Sensor
Sideways Scroll Settings
Menu Select
Run Screen Settings
Show BMP
Current File
Show More Files
Show Folder
Progress Bar
Dial And Button
Direction
Pulse Count
Long Press Count
Btn0 Long
Btn1 Long
Sleep Time
IP
Reset All
Dim Value
Dimming Mode
Preview Settings
Dial Scroll px
Auto scroll time
Auto Scroll px
Top Start Offset
Scroll Mode
Pulse Timer
File on Top Line

# 9 Construction

Yes, there are a few parts and a fair amount of wiring and soldering to do. If you aren’t comfortable soldering, find someone who is! The wiring harnesses are probably the most work to make, but they are essential to hook everything up. I will include a photo of the ones I make that should make it easier to duplicate. Looking at the schematic will help understanding what is connected to what. The 3D printed parts can be purchased from me if you can’t find anybody else to make them from the STL files. I print currently using PLA, so please don’t leave them in the sun, they will melt and deform if it gets too hot!

Also remember that the PCB makes building one of these much easier. There are two versions of the PCB, one that has a built-in 5V regulator and another that requires an external power supply. There are several versions of the 3D printer files for these cases. The external power supply version can supply more current for brighter LEDs. The internal one can supply about 1.5A but this is adequate for most night work. Using the wand as a light source might require more light, but building the wand is a little bit more complicated. Send me an email at martinnohr76 @ gmail.com if you want to order one. $40 + shipping for the one without the power supply and $45 + shipping for the one with the built-in power supply. Both of these include a programmed TTGO. The PCB’s without the TTGO are $20 and $25.

All of the screws are metric and should be available from a well-stocked hardware store. I got mine from Ace Hardware.

All of the electronic components and the aluminum channel are available from Amazon. They are likely also available from other vendors. I bought the aluminum shiny ones because I didn’t find the black anodized ones until later. Some people worry that the shiny aluminum will show in the final image. In practice I haven’t seen this, but I do plan to start using the black one after I finish using all the shiny ones I have in a box! I got the WS2812B LED strips from BangGood.com in China. Aliexpress.com also carries the WD2812B. Be aware that the shipping time from China can be quite long. Amazon is faster.

I am considering making a parts bag available with all the hardware parts needed. I buy them in quantity so it would be easy enough to put a bag together.

You can solder up a bunch of wires and connectors to connect everything inside the cpu/display box like I did for my first prototype. I have designed a printed circuit board holding all the parts and I can sell those for $50+shipping, it includes a programmed TTGO. For $30+shipping I can supply the PCB without the TTGO. There is still some wiring for the batteries and LED connectors, but it is much simpler when the dial, SD card reader, and TTGO are on a PCB. The PCB without the on-board power supply is $5 less, $45 with TTGO, $25 without.

The PCB version includes a level shifter to go from the ESP32 3.3 volt logic to the 5V specified for the WS2812B LED strips. If you build your own you can omit these level shifters. In testing we found that all our LED strips worked directly with 3.3V logic. There might be a rare LED strip that does not work however so we make no guarantees! Using a level shifter guarantees that the voltage levels meet the specifications.

## 9.1 Parts List

Some changes have been made to this latest version. A new battery design uses two 18650 batteries and a voltage regulator. There is also a PCB available with an on-board power supply. The original design using a USB charger has been abandoned because the USB chargers kept changing size and availability.

### 9.1.1 Electronic Parts

1. TTGO T1. https://www.amazon.com/ICQUANZX-T-Display-Bluetooth-Development-Arduino/dp/B07VNG9D52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
2. Optional TTGO with pre-soldered headers (almost never available though). https://www.cytron.io/c-wifi/p-ttgo-t-display-esp32-1.14-display-module-presolder-header (https://www.amazon.com/gp/product/B07DKD79Y9/ref=ppx_yo_dt_b_search_asin_title?ie=UTF8&psc=1)
3. Micro SD card reader if you don’t use the PCB. https://www.amazon.com/gp/product/B07BJ2P6X6/ref=ppx_yo_dt_b_search_asin_title?ie=UTF8&psc=1
4. Voltage regulator if you don’t use the on-board PCB or need more than 3 amps. Amazon.com: ( 6 Pcs ) MCIGICM LM2596 Buck Converter, DC to DC 3.0-40V to 1.5-35V Step Down Power Supply High Efficiency Voltage Regulator Module: Electronics (https://www.amazon.com/dp/B06XZ1DKF2?psc=1&ref=ppx_yo2_dt_b_product_details)
5. Rotary encode switch if you don’t use the PCB which includes it. https://www.amazon.com/gp/product/B07DM2YMT4/ref=ppx_yo_dt_b_search_asin_title?ie=UTF8&psc=1
6. 5 pin, 4 pin, and 3 pin connectors. The 5 pin is not used with any of the PCB versions. https://www.amazon.com/gp/product/B07GGPQXFC/ref=ppx_yo_dt_b_search_asin_title?ie=UTF8&psc=1 https://www.amazon.com/gp/product/B075K3M1TB/ref=ppx_yo_dt_b_search_asin_title?ie=UTF8&psc=1 https://www.amazon.com/gp/product/B075K6N7DF/ref=ppx_yo_dt_b_search_asin_title?ie=UTF8&psc=1
7. LED channel, Amazon makes you buy at least 6 of these, maybe somebody sells singles. https://www.amazon.com/gp/product/B01LL2SLME/ref=ppx_yo_dt_b_search_asin_title?ie=UTF8&psc=1
8. WS2812B LED strips. https://www.amazon.com/gp/product/B07BKQZLDL/ref=ppx_yo_dt_b_search_asin_title?ie=UTF8&psc=1
9. Battery connectors for the 18650 battery in handle versions. Amazon.com: uxcell 20 Pairs AA Battery Positive Negative Conversion Spring Contact Nickeling Plate 12mmx12mmx0.3mm : Automotive (https://www.amazon.com/dp/B07HRWS4W2?psc=1&ref=ppx_yo2_dt_b_product_details) or Amazon.com: uxcell 10 Pairs AA AAA Batteries Metal Battery Spring Contact Plate Replacement for Remote Control Battery Charger : Electronics (https://www.amazon.com/uxcell-Pairs-Silver-Battery-Spring/dp/B00GN3PN46)
10. LDR (light dependent resistor) for the optional light sensor. eBoot 30 Pieces Photoresistor Photo Light Sensitive Resistor Light Dependent Resistor 5 mm GM5539 5539: Amazon.com: Industrial & Scientific (https://www.amazon.com/gp/product/B01N7V536K/ref=ppx_yo_dt_b_search_asin_image?ie=UTF8&psc=1)
11. Heat sinks for the voltage regulator and inductor coil. Only needed if you buy the PCB direct from pcbway.com. Amazon.com: Easycargo 20pcs Small Mini Heatsink Kit + Thermal Conductive Adhesive Tape, Mini Cooler Aluminum Heat Sink for Cooling VRM GPU Stepper Driver MOSFET VRam Regulators (8.8mmx8.8mmx5mm) : Electronics (https://www.amazon.com/gp/product/B079FQ22LK/ref=ppx_yo_dt_b_search_asin_title?ie=UTF8&psc=1)
12. 8mm threaded shaft for spinner handle.
13. Various 2mm and 3mm screws to hold things in place.
14. Skateboard ball bearings for spinner handle. FKG 608-2RS 8x22x7mm Skateboard Bearings, Deep Groove Ball Bearing Double Rubber Seal Bearings Pre-Lubricated 10 Pcs: Amazon.com: Industrial & Scientific (https://www.amazon.com/FKG-608-2RS-8x22x7mm-Skateboard-Pre-Lubricated/dp/B085XTWX1Z)

### 9.1.2 3D Printed Parts

1. Battery holder
2. Base plate for LED strips
3. Power supply base and cover for the PCB without the on-board power supply
4. LED strip end protectors
5. ARCA tripod clamp
6. Battery end sliding cover
7. Handle
8. TTGO case top and bottom, there are two versions for the two PCB versions
9. Knob for rotary dial
10. Spinner handle
11. Butterfly parts for attaching battery case to handle and base plate

### 9.1.3 Software and Libraries

The compiled bin file is available on the GitHub entry for this project if you don’t want to collect all these files and compile the code. It can be built with the Arduino IDE, but I personally prefer Microsoft Visual Studio Community version along with the Visual Micro extension for Arduino, which is priced very reasonably. Microsoft Visual Code can also be used with the added Arduino add-in.

Most of the time the latest versions of the libraries will work, the only exception is the SdFat library. Versions after 2.0.7 are not compatible with earlier versions. This will be fixed in the future.

The GitHub entry has the schematic and other plans for the case.

https://github.com/MartinNohr/MagicImageWand

1. Arduino IDE, or Microsoft Visual Studio with Visual Micro, or VisualCode set up for TTGO esp32.
2. ESP32 support libraries for TTGO T1
3. Bodmer’s tft_espi display library
4. FastLED library
5. ESP32Encoder by Kevin Harrington
6. SdFat by Bill Greiman, use version 2.0.7, the latest version is not compatible yet
7. There is a wiki on the site explaining how to get all the libraries for the Arduino IDE

## 9.2 Wiring Harnesses Without PCB

These are somewhat time consuming to make. Soldering skills are required. See pictures on GitHub and thingiverse.com for what they look like. Going forward this version isn’t planned to be supported for very long. Development effort is used on the new on-board power version. It will still be possible to add more power to the LED’s if needed by running power lines directly to the LED’s.

1. Internal, for SD card reader, level shifter (optional but no guarantees), LED/Power, and rotating button.
2. Battery and LED’s.
3. Rotating button.

## 9.3 Assembling the on-board Power Supply PCB version

The folder MagicImageWand/PCB_OnBoardPower at main · MartinNohr/MagicImageWand (github.com) (https://github.com/MartinNohr/MagicImageWand/tree/main/PCB_OnBoardPower) has all the 3D files and some photos showing how the assembly looks. More photos are in this document along with descriptions.

### 9.3.1 3D Parts Printing Orientation

The parts are best printed as shown here. The battery case might need a raft if your printer bed adhesion is not strong enough. The handle needs supports. Two sets of the wedge joiners are needed. The short ones are under the handle and the longer ones are above the LED aluminum extrusion base.

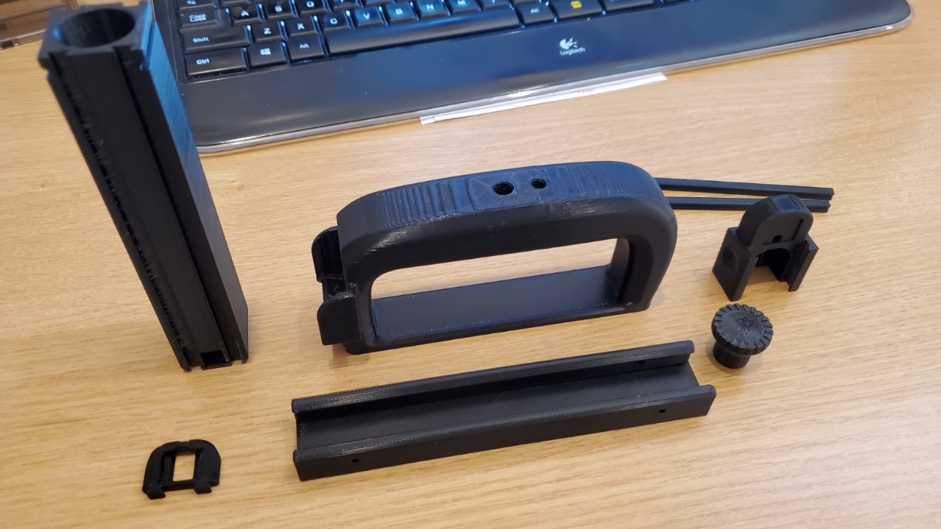
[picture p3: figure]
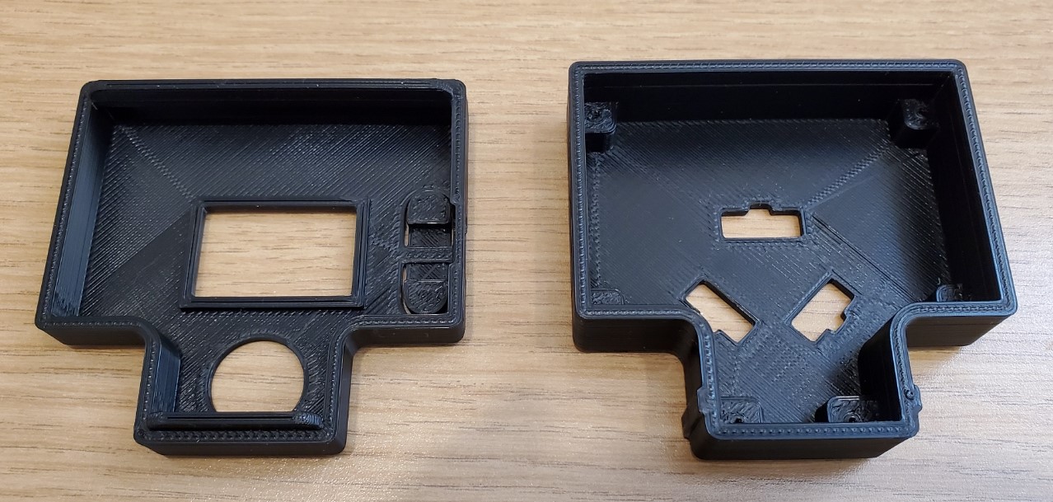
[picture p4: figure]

### 9.3.2 PCB Preparation

The TTGO is mounted on the sockets as shown. It can be connected with the USB port for programming and testing. The 3 pin LED wires and the 4 pin power wires are cut to an appropriate length and soldered to the PCB. Note that the power uses 2 wires for ground and +5V. These wires are folded under the PCB after the connecters are mounted in the bottom holes of the case. The connectors started at an angle and then pulled through until the wings engage the case. The round audio connector next to the SD reader is not used at this time, but there had to be a hole for it.

It is not necessary to use the connectors, you can simply solder the wires instead. I like the ability to take things apart later, so I used connectors.

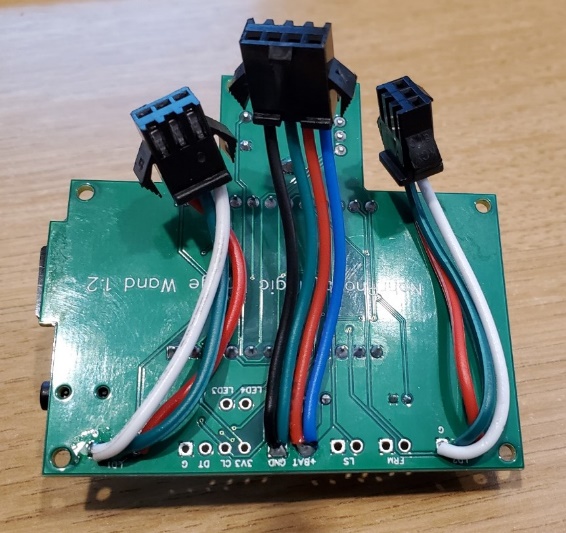
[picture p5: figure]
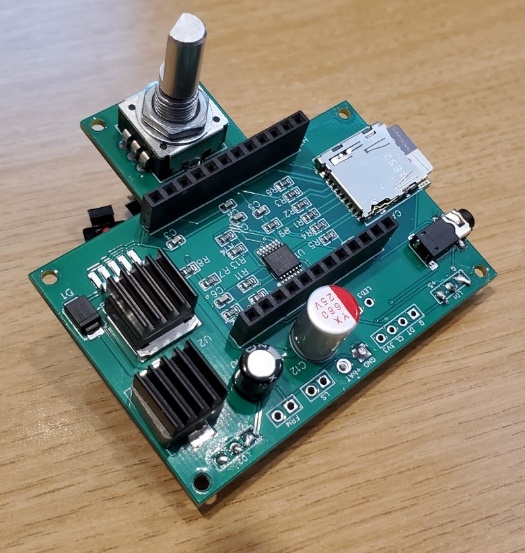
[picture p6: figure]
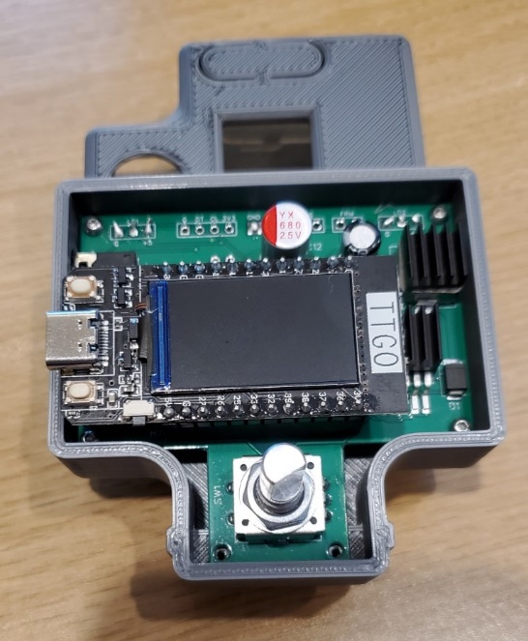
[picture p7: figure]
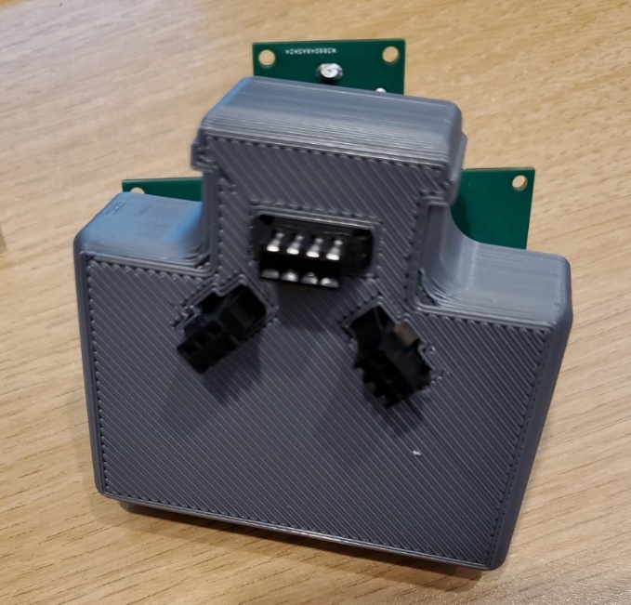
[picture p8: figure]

### 9.3.3 Preparing the Battery Case

The battery case needs a negative battery connector (the one with the spring) inserted in the slot with the solder tab up. Make sure the retaining clips on the connector have been flattened, they are not needed. This can be tricky, use a needle nose pliers and make sure it is seated all the way up. The tab will appear in the slot. This is where the negative wires from the 4 wire connector are soldered. The positive wires are soldered to the long wire from the other end that is passed through the slot between the handle and the battery case. Do not attach the wires until the handle has been attached to the battery case. The slots for the connector might need to be cleaned with a knife first. Insert the connector and push it all the way down with a screwdriver or other tool until it is seated as shown. Bend the tab out so that a wire can be soldered to it.

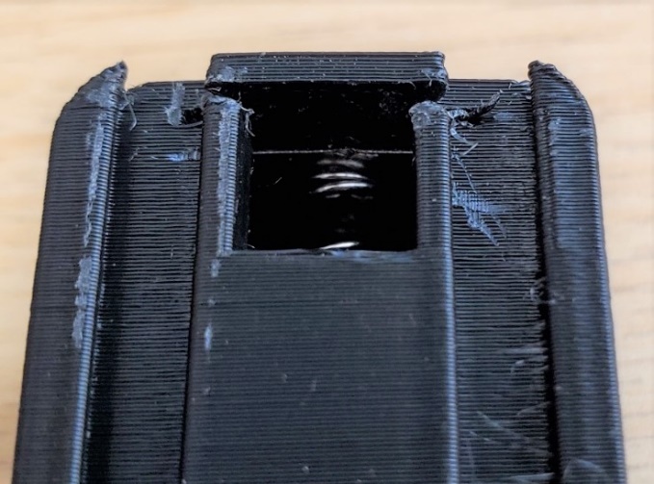
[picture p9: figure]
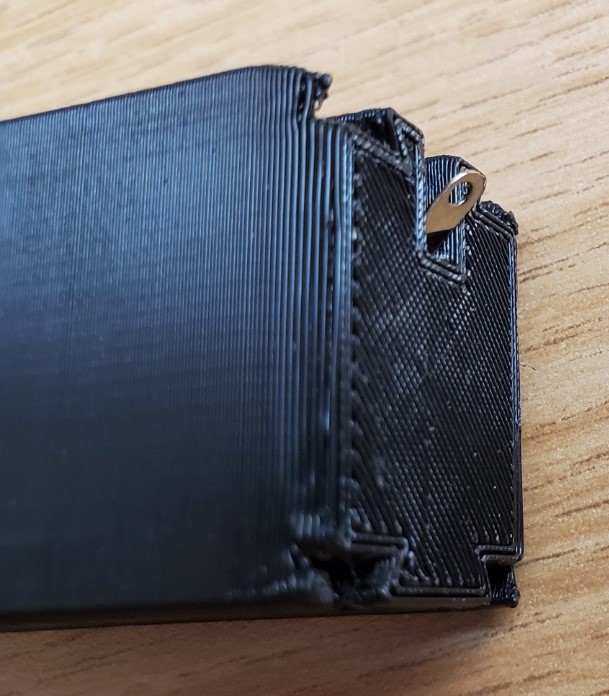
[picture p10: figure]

The negative wires from the 4-wire connector will be soldered to the tab. Do this carefully to avoid melting too much of the battery case!

### 9.3.4 Power Connector

The power connector uses a positive and negative battery connector that have been soldered back-to-back with a couple of spots of solder on the edges. The spring side is loaded against the handle. Solder a wire onto the connector that is long enough to go through the hole in the base of the handle. This will be connected to the 4 pin wire connector leading to the TTGO case. The second picture shows this assembled to the battery case. The spring is on the back side where it pushes onto the depression on the handle. Solder an 8” piece of wire to the connector as shown.

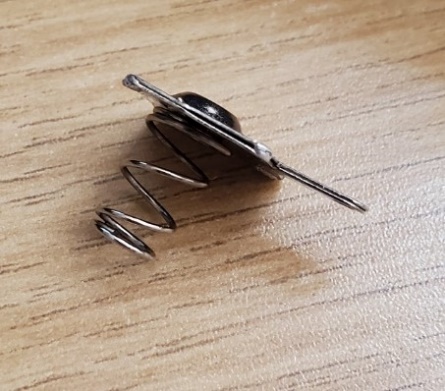
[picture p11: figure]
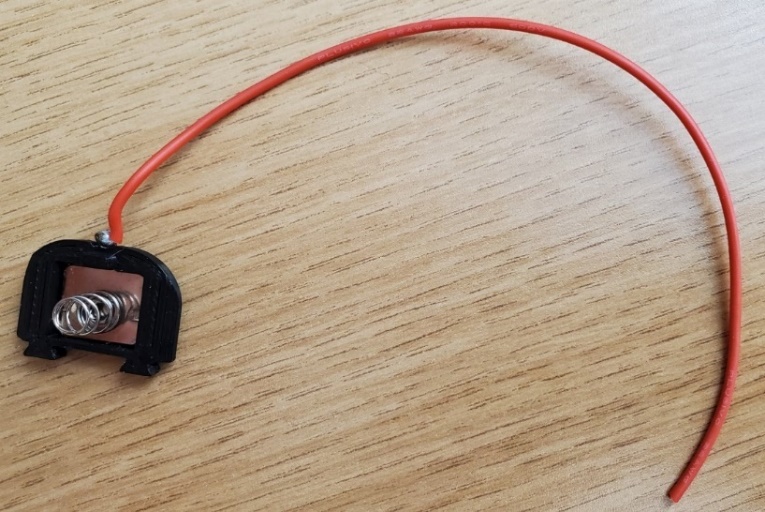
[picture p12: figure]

### 9.3.5 Handle to Battery Case

Using two of the wedge joiner strips the battery case can be attached to the handle. The front (where the TTGO case is) should line up with the battery case. This might be really tight or fairly easy depending on your 3D printers calibration and accuracy. File and trim carefully if necessary. The wedge joiners could also be printer in a slightly reduced size if they are too tight. When the position is correct a little glue can be applied to hold it if necessary.

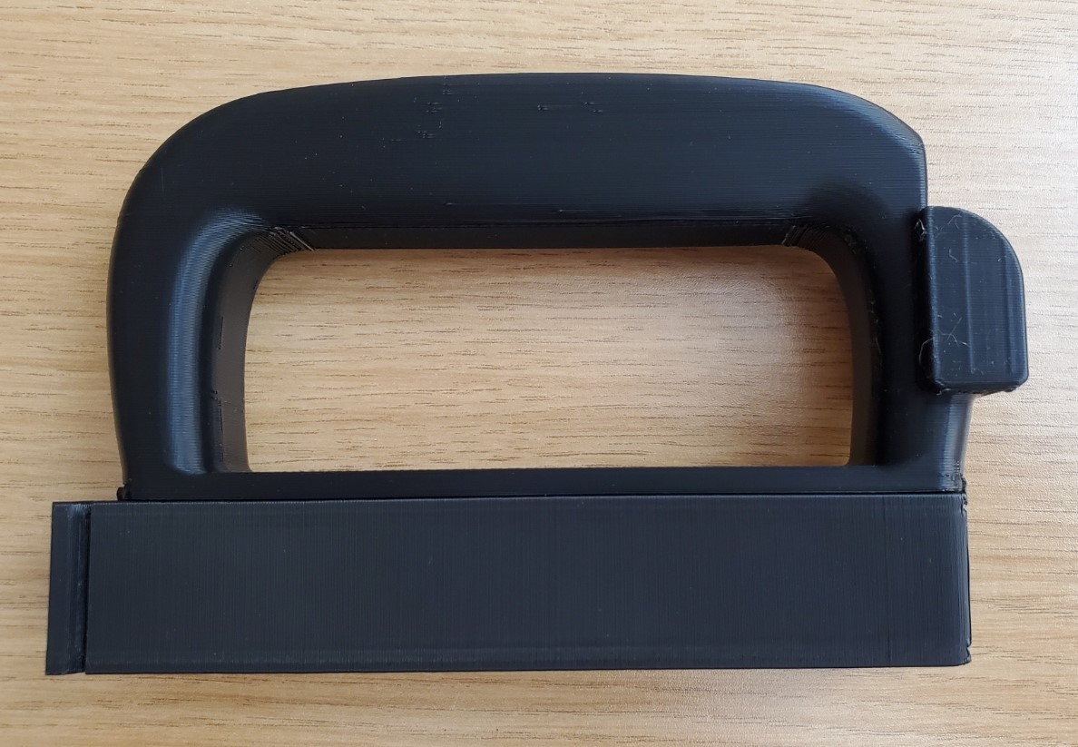
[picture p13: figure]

### 9.3.6 Battery End Connector

This connector slides on the end of the battery compartment. Sliding the battery end connector acts like a cheap power switch. It needs two positive battery connectors that are connected with a short piece of wire. Be careful soldering, PLA melts easily! Put a little glue behind the top connector to hold it in place, remember to solder the wire on it first because there isn’t room to do that after it is placed into position.

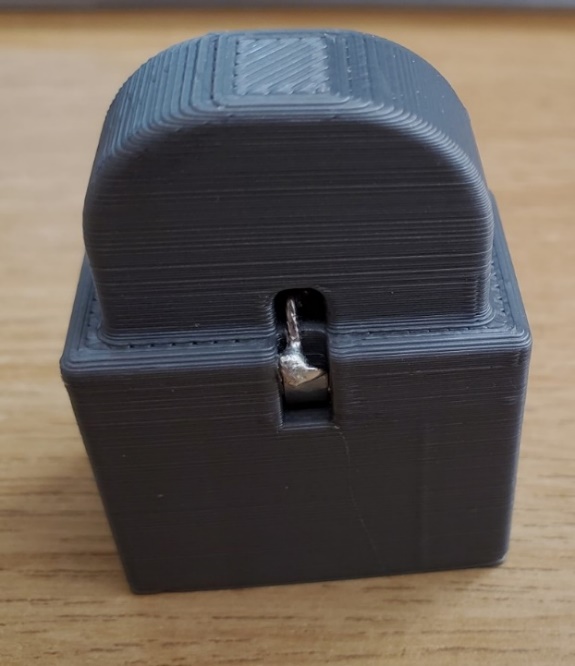
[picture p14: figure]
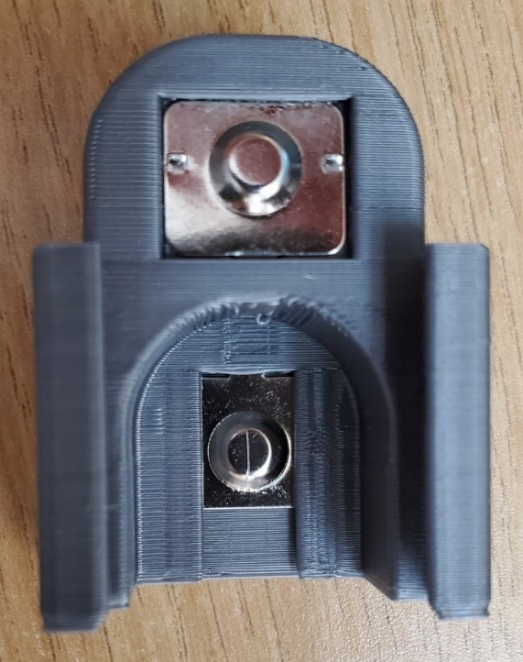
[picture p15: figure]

### 9.3.7 Adding the LED Extrusion Holder

The LED holder is added using two more of the wedge strips. Again, this might be tight, file or trim as necessary. Align the holder with the middle slots under the big hole on the top of the handle. This will make the spinner handle exactly in the middle of a two strip version of the wand. Apply glue to hold things in place. The screws to hold the LED extrusions are 3mm. Tapping with a 3mm tap will make them fit better, but the screws will cut their own thread.

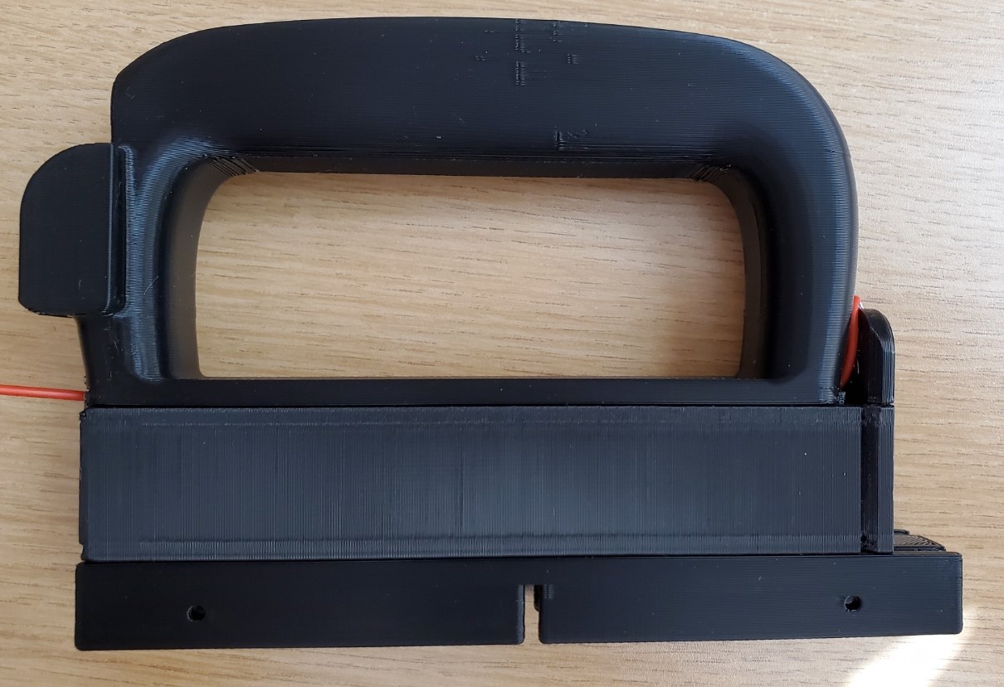
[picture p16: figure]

### 9.3.8 Add Power Connector to Battery Case

Next the power connector is pressed onto the end of the battery case. Insert the metal connector and then press the assembly onto the end while threading the wire through the center hole under the handle. The connector should be a tight fit, if too tight trim carefully. Glue can be added if necessary. Make sure the connector is flush with the battery case, this is necessary so the end connector will slide in the slots. Do not use glue on the metal connector, it must be free to push against the spring to ensure a good connection.

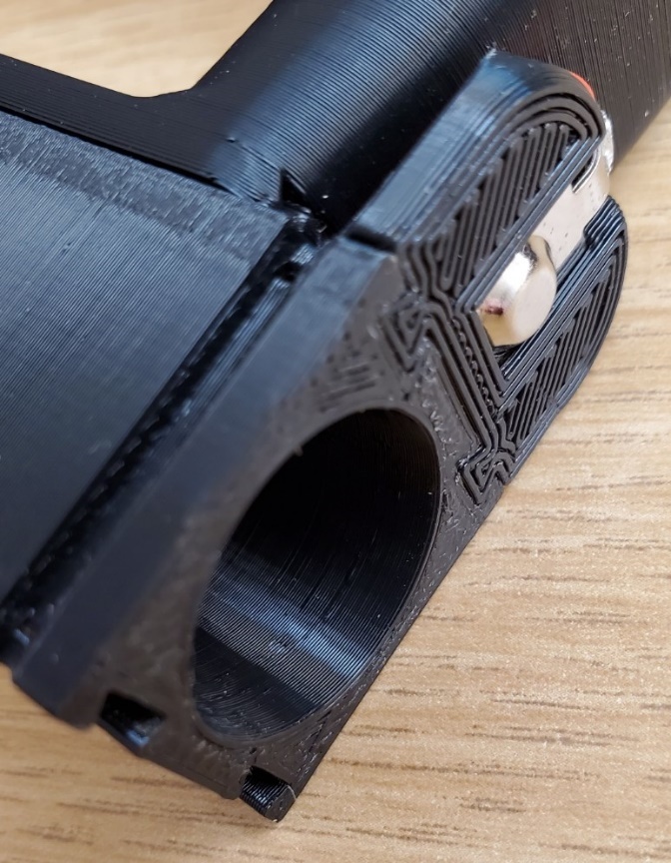
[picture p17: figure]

### 9.3.9 Preparing the LED Strips

Unsolder the connectors from both ends of the WS2812B LED strips if they came with them on. The factory ones are backwards from what we need since we used the male connector on the TTGO case. Cut the new female connector wires diagonally so they can be attached going out sideways as shown in the photo below. Solder them carefully!

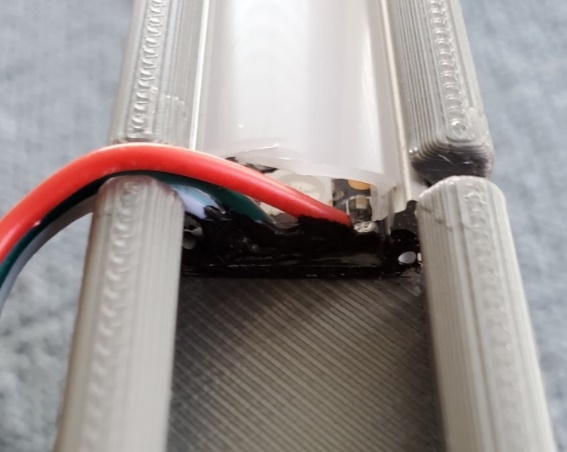
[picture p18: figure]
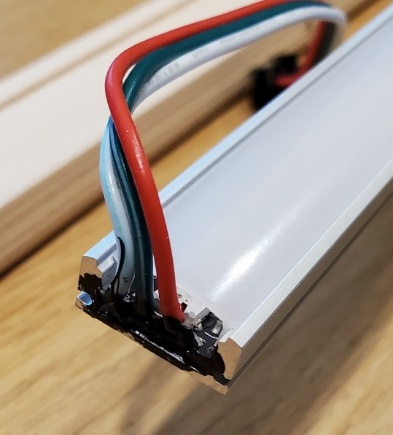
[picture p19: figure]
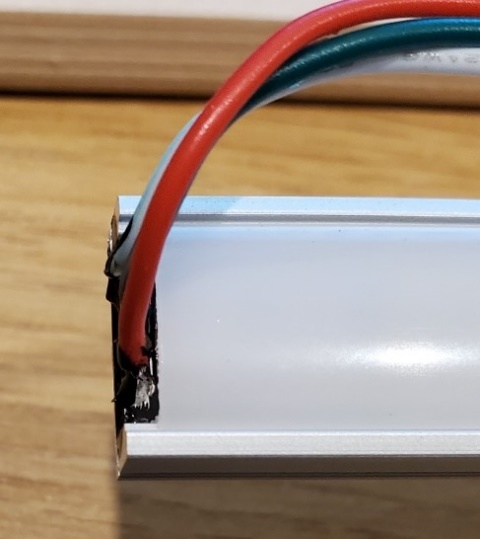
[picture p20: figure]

### 9.3.10 Attach TTGO Case to Handle

The TTGO case is simply pushed down onto the handle mount, it might be tight the first time, file or trim if necessary. Once attached the battery and LED’s can be attached. The batteries are inserted in the battery case negative end first. Pushing the battery end connector all the way down should start the system. If it doesn’t work, check all the battery wires and connectors to make sure power is getting to the board.

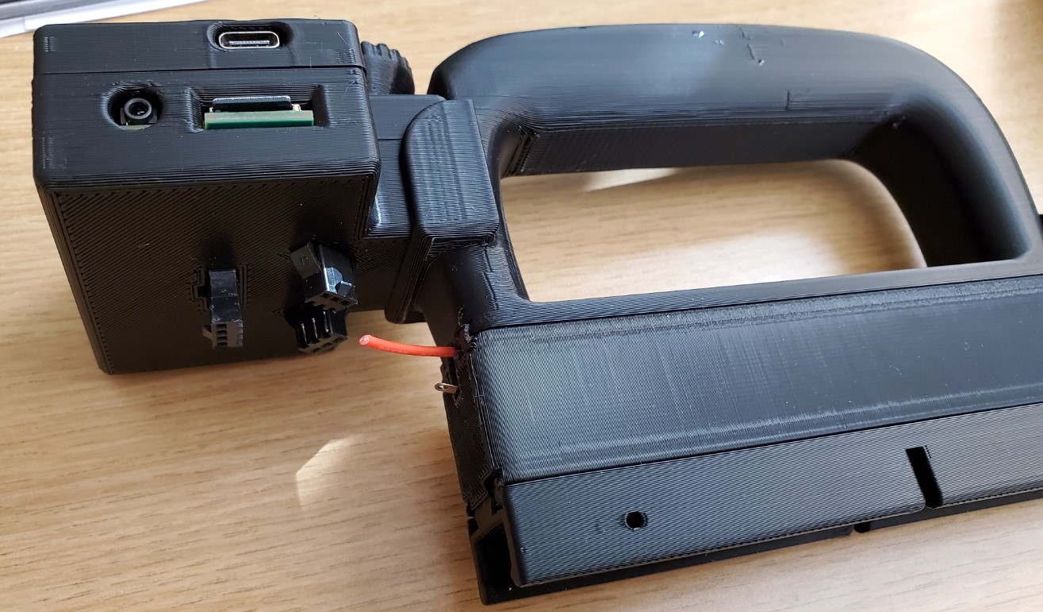
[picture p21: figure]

### 9.3.11 Optional Spinner Handle and Knob

The spinner handle is useful when two LED strips are attached. It uses an 8mm threaded rod and two roller blade ball bearings. The rod is held to the round handle with 8mm nuts, you can use two or a single nylon lock type nut. The optional knob (there is a large one and a small one, your choice) for spinning is screwed on the end and held with a nut and washer. The 8mm rod can be cut to whatever length you prefer.

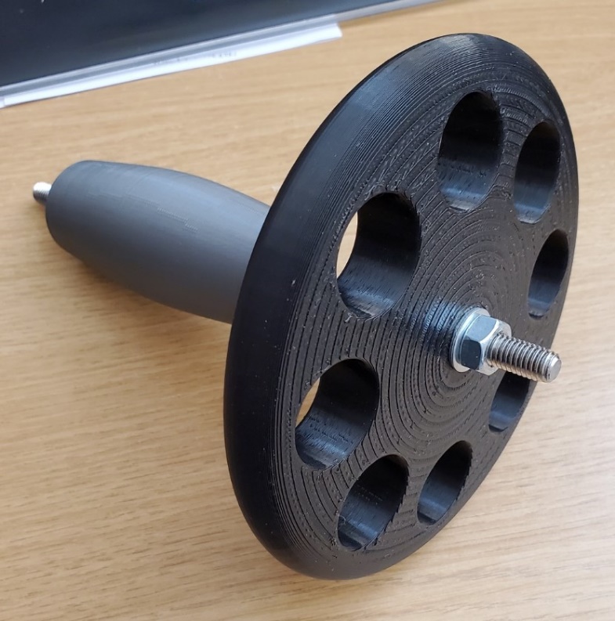
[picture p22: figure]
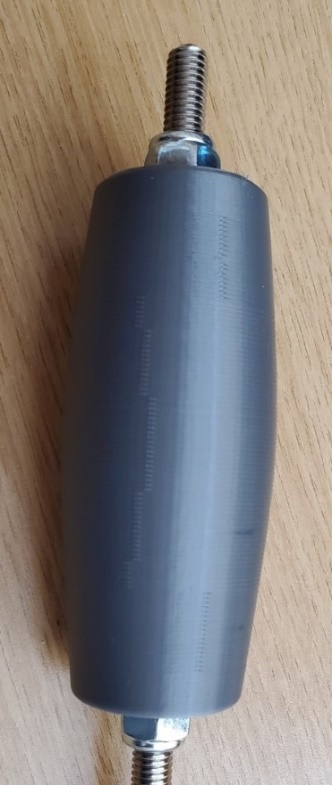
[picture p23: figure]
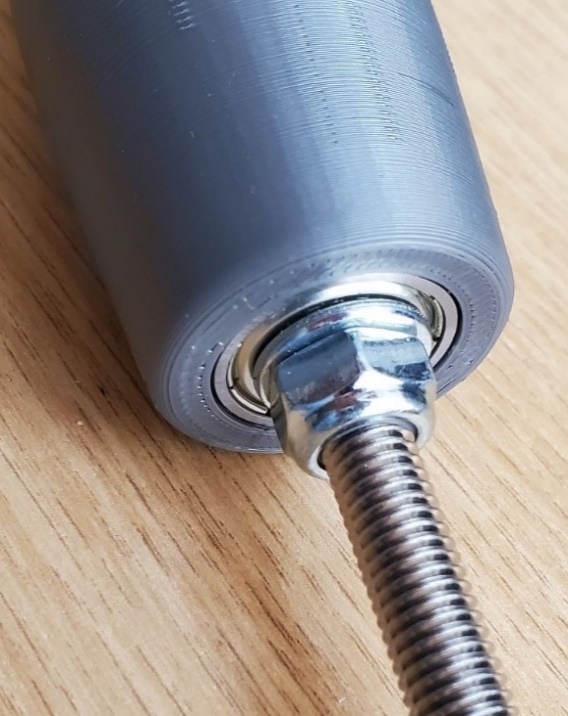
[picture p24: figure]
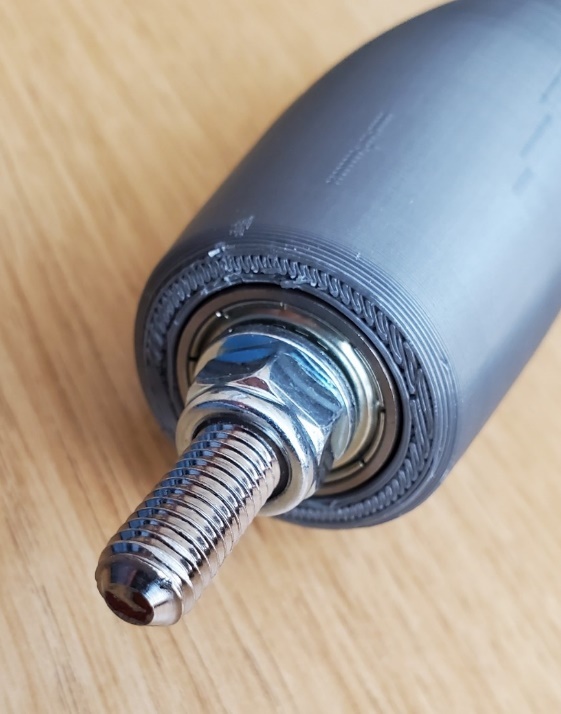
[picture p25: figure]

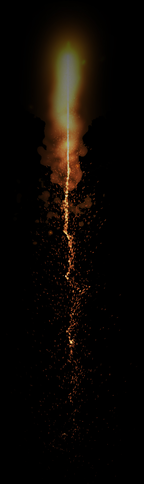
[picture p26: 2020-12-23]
ImageWandSampleImages/144/Fire/FireSparkle.bmp

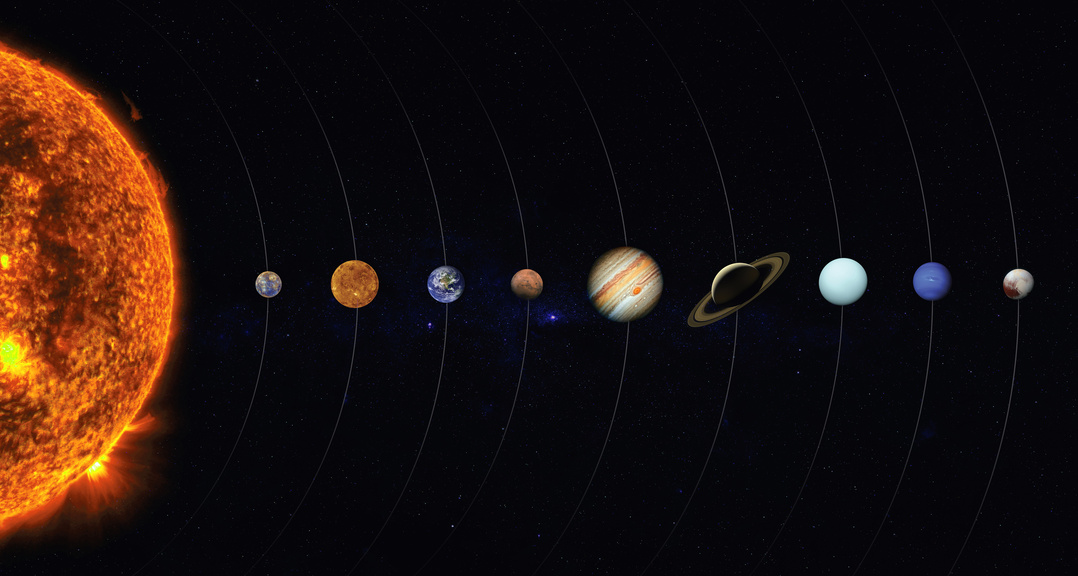
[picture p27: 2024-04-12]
ImageWandSampleImages/source images/SolarSystem/solarsystem.jpg

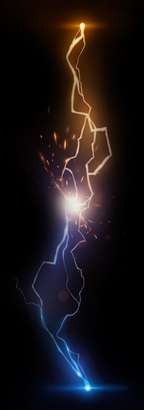
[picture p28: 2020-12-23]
ImageWandSampleImages/144/Lightning/LightningBlueOrange5.bmp

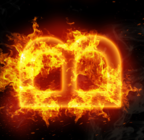
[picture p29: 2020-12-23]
ImageWandSampleImages/144/Fire-Alphabet/B.bmp

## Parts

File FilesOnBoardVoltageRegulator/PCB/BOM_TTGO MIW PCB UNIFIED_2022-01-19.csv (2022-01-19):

ID | Name | Designator | Footprint | Quantity | Manufacturer Part | Manufacturer | Supplier | Supplier Part | Price
1 | 100 | R13,R14,R10,R11 | R0603 | 4 | 0603WAF1000T5E | UniOhm | LCSC | C22775 | 0.001
2 | PJ-2342-SMT | CN1 | AUDIO-SMD_PJ-2342-SMT | 1 | PJ-2342-SMT | XKB Enterprise | LCSC | C397356 | 0.134
3 | 220uF | C10 | CAP-TH_BD5.0-P2.00-D0.8-FD | 1 | 220uF 16V 6.3*7 | ValuePro | LCSC | C43340 | 0.018
4 | DM3AT-SF-PEJM5 | CARD1 | SD-SMD_DM3AT-SF-PEJM5 | 1 | DM3AT-SF-PEJM5 | Hirose | LCSC | C114218 | 1.062
5 | 33uH | L1 | IND-SMD_L11.5-W10.0_SMMS1040 | 1 | YSPI1050-330M | YJYCOIN | LCSC | C497900 | 0.337
6 | 74HCT125PW,112 | U1 | TSSOP-14_L5.0-W4.4-P0.65-LS6.4-BL | 1 | 74HCT125PW,112 | Nexperia | LCSC | C545657 | 0.185
7 | 680uF | C12 | CAP-TH_BD8.0-P3.50-D0.6-FD | 1 | SPT1EM681F12OR | Yunxing | LCSC | C698148 | 0.304
8 | PEC11R-4220F-S0012 | SW1 | SW-TH_PEC11R-4XXXF-SXXXX | 1 | PEC11R-4220F-S0012 | BOURNS | LCSC | C143817 | 1.911
9 | B2100-13-F | D1 | SMB_L4.6-W3.6-LS5.3-RD | 1 | B2100-13-F | DIODES | LCSC | C110479 | 0.203
10 | LM2596R-5.0 | U2 | TO-263-5_L10.2-W8.6-P1.70-LS14.4-TL | 1 | LM2596R-5.0 | HTC | LCSC | C77782 | 1.12
11 | 510k | R8 | R0603 | 1 | 0603WAF5103T5E | UniOhm | LCSC | C23192 | 0.002
12 | 100nF | C6,C4,C1,C2,C3 | C0603 | 5 | CL10B104KC8NNNC | SAMSUNG | LCSC | C15725 | 0.007
13 | 470k | R12 | R0603 | 1 | 0603WAF4703T5E | UniOhm | LCSC | C23178 | 0.001
14 | 120k | R7 | R0603 | 1 | 0603WAF1203T5E | UniOhm | LCSC | C25808 | 0.001
15 | A2541HWV-12P | H6,H7 | HDR-TH_12P-P2.54-V_A2541HWV-12P | 2 | A2541HWV-12P | Changjiang Connectors | LCSC | C225509 | 0.279
16 | 4.7nF | C5 | C0603 | 1 | CC0603KRX7R9BB472 | YAGEO | LCSC | C106218 | 0.003
17 | 20k | R4,R5,R1,R6,R3,R2,R9 | R0603 | 7 | 0603WAF2002T5E | UniOhm | LCSC | C4184 | 0.002

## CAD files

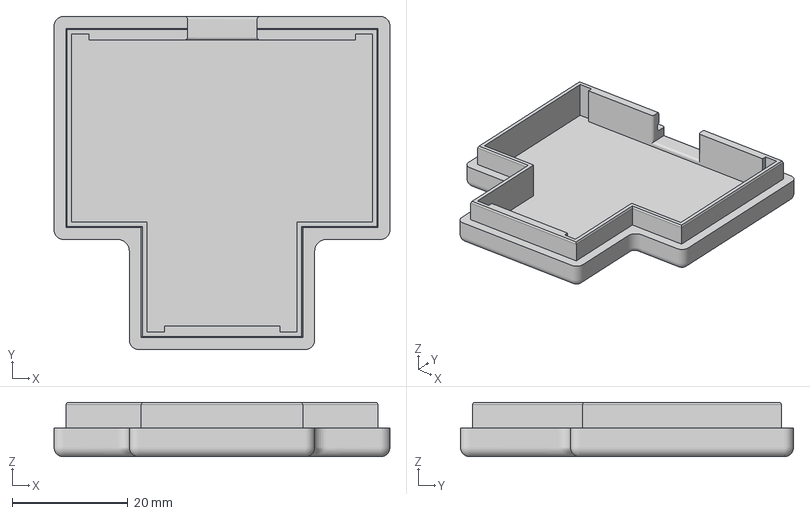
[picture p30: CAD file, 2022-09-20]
FilesExternalVoltageRegulator/TTGO Bottom.3mf
58.0 x 57.5 x 9.40 mm

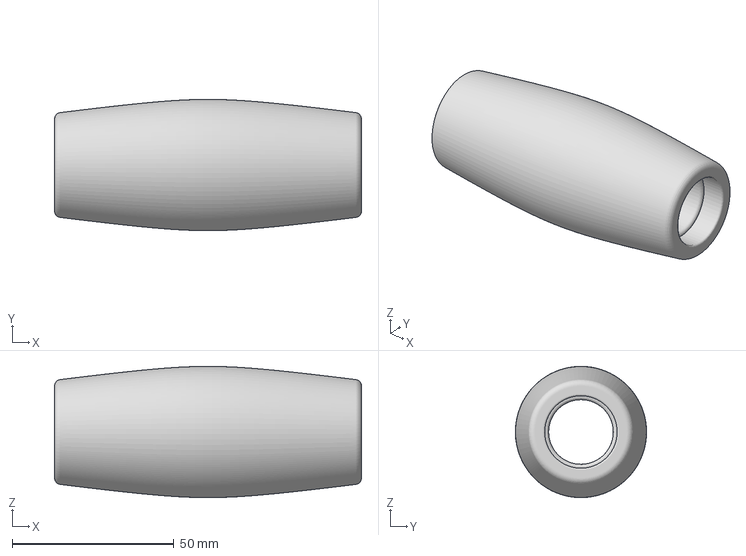
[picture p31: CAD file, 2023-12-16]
FilesOnBoardVoltageRegulator/RotatorHandle.3mf
95.0 x 40.6 x 40.6 mm

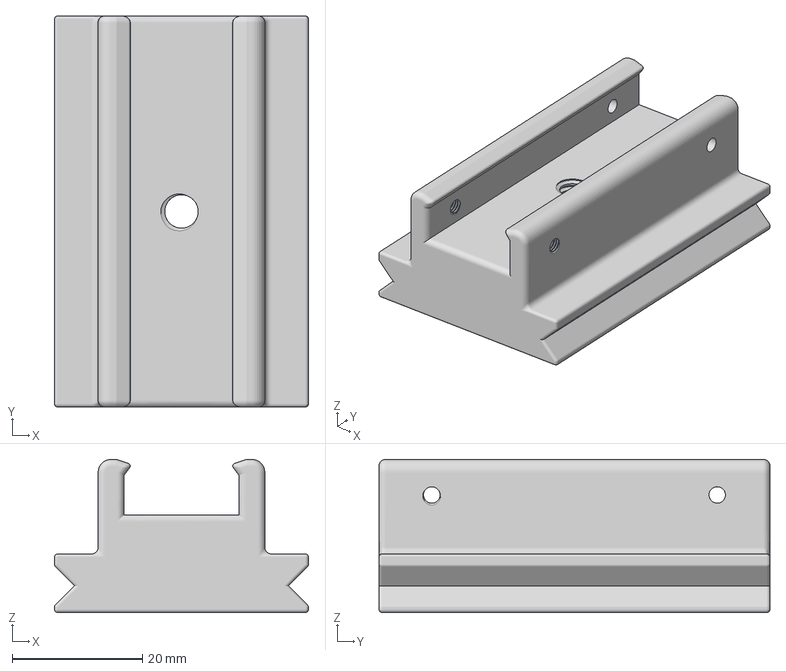
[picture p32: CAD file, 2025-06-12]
MIWS3/ARCA tripod.3mf
39.0 x 60.0 x 23.5 mm

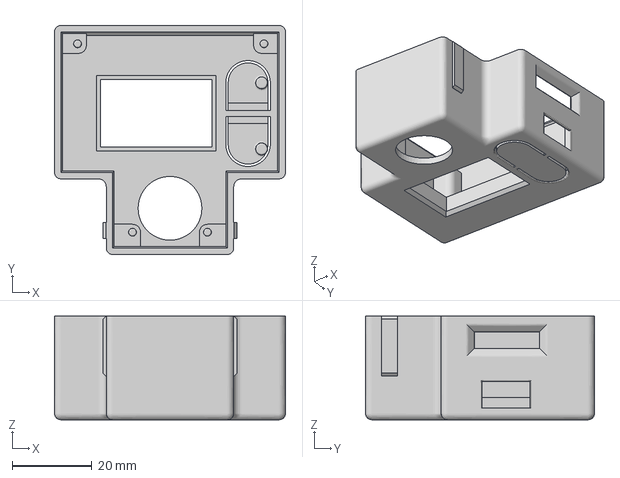
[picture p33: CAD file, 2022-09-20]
FilesExternalVoltageRegulator/TTGO Top.3mf
58.0 x 57.5 x 26.0 mm

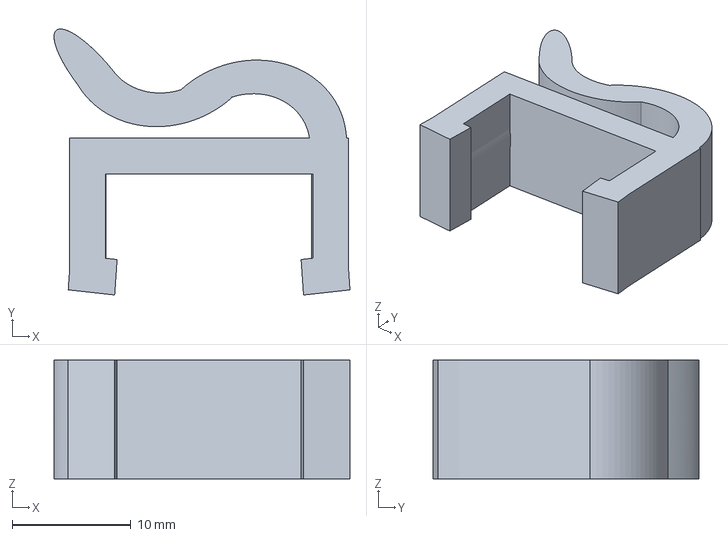
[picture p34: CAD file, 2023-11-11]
FilesOnBoardVoltageRegulator/wireclip.3mf
24.9 x 22.4 x 10.0 mm

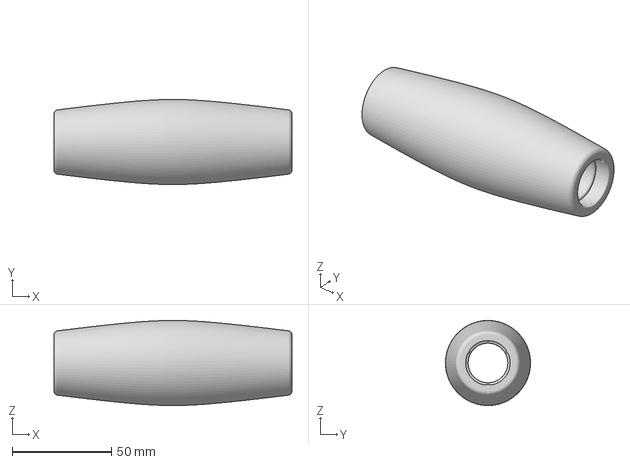
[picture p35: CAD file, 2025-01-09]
MIWS3/RotatorHandle.3mf
120.0 x 42.9 x 42.9 mm

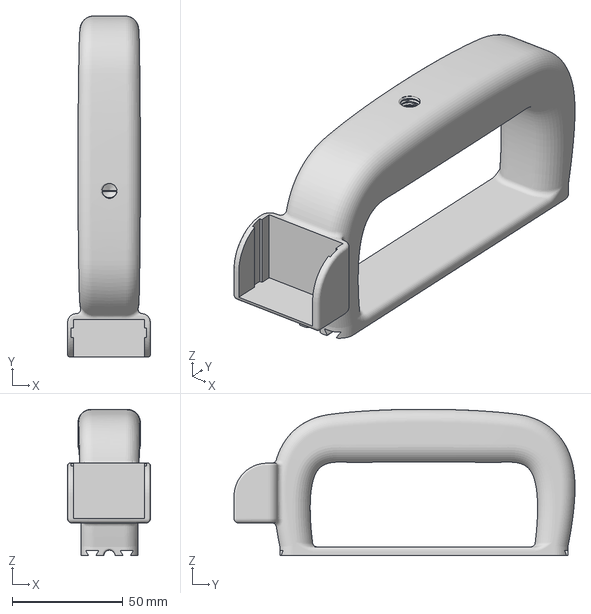
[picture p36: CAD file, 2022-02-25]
FilesExternalVoltageRegulator/5A Handle.3mf
37.4 x 153.9 x 66.1 mm

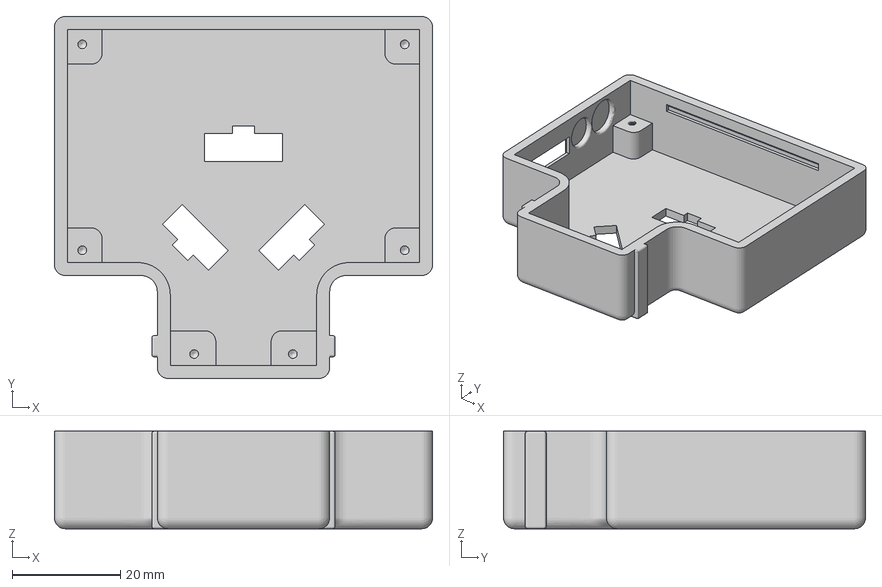
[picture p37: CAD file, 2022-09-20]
FilesOnBoardVoltageRegulator/MIWPS Bottom.3mf
69.8 x 66.8 x 18.0 mm

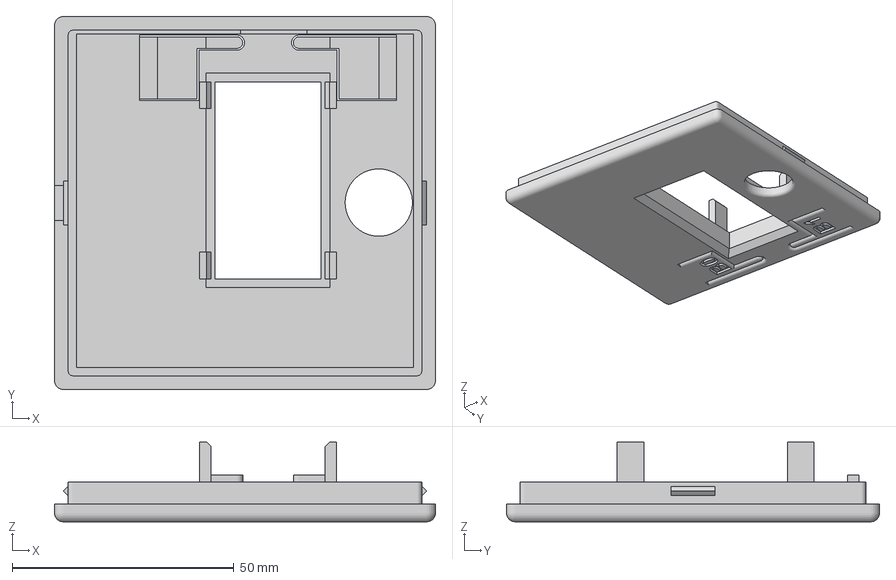
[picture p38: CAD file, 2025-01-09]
MIWS3/MIW3Top.3mf
86.0 x 84.2 x 18.0 mm

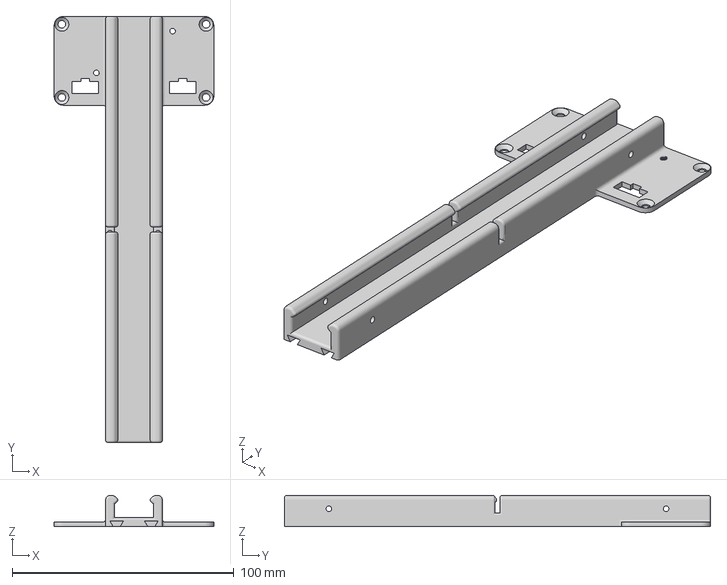
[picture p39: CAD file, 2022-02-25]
FilesExternalVoltageRegulator/5A Base.3mf
72.0 x 192.0 x 14.0 mm

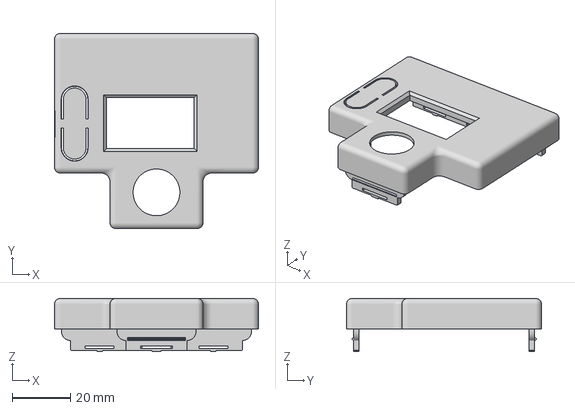
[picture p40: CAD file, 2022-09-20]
FilesOnBoardVoltageRegulator/MIWPS Top.3mf
69.8 x 66.8 x 18.2 mm

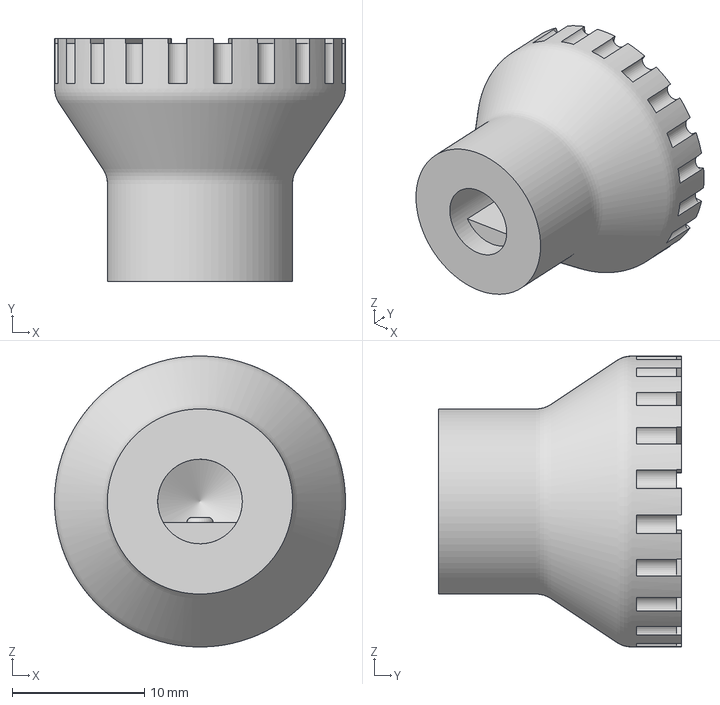
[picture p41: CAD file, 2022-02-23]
FilesExternalVoltageRegulator/MIWPS Button.3mf
22.0 x 18.4 x 22.0 mm

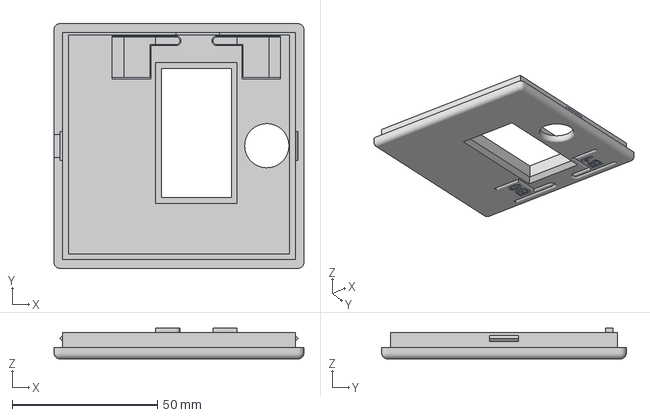
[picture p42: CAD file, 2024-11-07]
MIWS3/BoxTop.3mf
86.0 x 84.2 x 10.6 mm

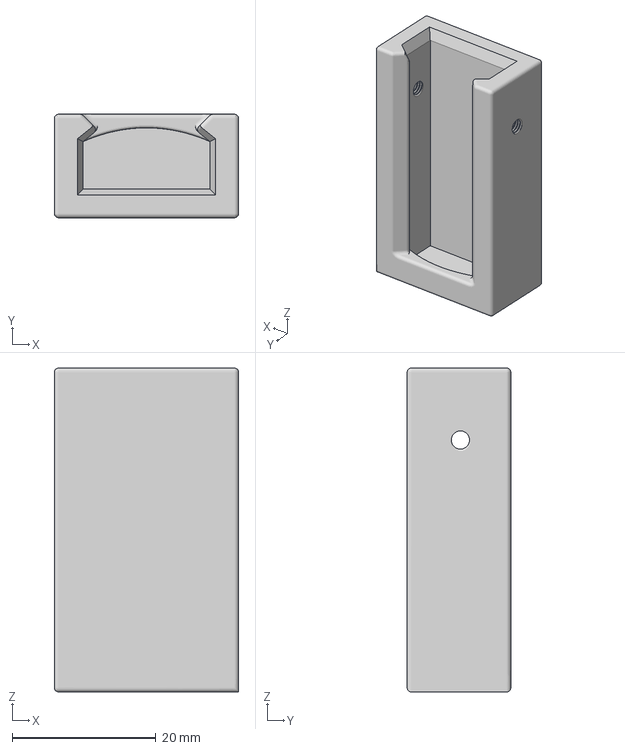
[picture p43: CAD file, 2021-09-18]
FilesExternalVoltageRegulator/end bumper.3mf
25.6 x 14.4 x 45.0 mm

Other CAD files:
MIWS3/rotator wheel.3mf
FilesOnBoardVoltageRegulator/MIWPS Button.3mf
FilesOnBoardVoltageRegulator/strip tripod arca.3mf
MIWS3/MIW3BoxBottom.3mf
FilesExternalVoltageRegulator/18650 Dual Battery Handle 5A Reg v20.f3z
FilesExternalVoltageRegulator/18650body.3mf
FilesExternalVoltageRegulator/18650end.3mf
FilesExternalVoltageRegulator/Buck Regulator 5A v9.f3d
FilesExternalVoltageRegulator/Joiner.3mf
FilesExternalVoltageRegulator/MIWPS Button v15.f3d
FilesExternalVoltageRegulator/SB CPU Case TTGO v43.f3d
FilesExternalVoltageRegulator/WireCover.3mf
FilesExternalVoltageRegulator/strip tripod arca.3mf
FilesOnBoardVoltageRegulator/18650 Dual Battery Handle Builtin PS V2 v37.f3d
FilesOnBoardVoltageRegulator/18650 HandlePS.3mf
FilesOnBoardVoltageRegulator/18650 Rotator handle v4.f3d
FilesOnBoardVoltageRegulator/18650body.3mf
FilesOnBoardVoltageRegulator/18650end.3mf
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

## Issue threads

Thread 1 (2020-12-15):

progress and suggestions

MartinNohr, 2020-12-15:
Let's continue our discussions from the lightwand post here.
I'll start by saying that I now have my test code on the TTGO getting closer.
- SD card works, even with exFat formatted cards larger than 32GB.
- Rotary dial switch works
- LED strip works
I have some text working on the display, but I have some work left to do to get the full menu system up and running. Later this week if I don't get too many interruptions.
I also have a schematic that I'll post tomorrow.
I'll have the code up as soon as it works.

DaveStu, 2020-12-19:
Hi gentlemen, hope all are well. It's been a while, been busy with covid life and the ever changing rules.
Anyway, seems much has been progrssed, the excitement is overwhelming.
Haven't had much time to design enclosures and attaching mechanisms, though I did look at Dirks design on previous thread and looked great, hows that going?
Whilst I've been away/waiting, ordered another LED strip, the temptation for a £5 deal with coupons was too good pass.

So, are we still using Arduino to compile?

MartinNohr, 2020-12-20:
Sounds fun. :-(
It can be compiled and it is running more or less on the TTGO now. I have a lot of display issues to resolve, but most of them should be done in the next couple of days. The LED's are running ok as far as I can tell.
I'm going to improve the fonts a bit, I think they are a little bit too small. I can read them ok, but I have really good eyes for a 70+ old engineer. I know a lot of my friends won't be able to read them.
As soon as I get that stuff done I'll add the preview feature and then start on other ideas that we think (or thought) of.

MartinNohr, 2020-12-20:
We've had a number of our friends get Covid now, One died, he was 5 years older than me. Kind of scary. Everybody else we know has recovered. We mostly stay at home. I'm retired so it hasn't affected me very much really. We have started going to the store for food more now. I have about a 1/4 acre garden so during the summer we grow a lot of our own food, but now it is winter and the vegetables don't grow very well. We have a lot in the freezer, but fresh food is nice.

dirkessl, 2020-12-20:
@MartinNohr yes, covid keeps us all busy. I'm sorry for you losing a friend due to it. A close friend of mine also had it and recovered, just his sense of taste hasn't come back, yet. As I live in the middle of Munich, I have no chance of growing my on vegetables, but this would be wonderful if I would be able to do that.

dirkessl, 2020-12-20:
I have put all the info from the Word file into the wiki here, this makes it easier to maintain (at least for me :-) ). Once I will have the hardware running, I will put examples pictures for the inbuilt patterns and other stuff. BOM list needs to be updated.

I have also designed and printed a new case, as on my previous case the TTGO was upside down. Everything fits neatly inside now and there is enough room for the wiring harness. ToDo on the case are snap connectors to make the case close without screws.

I received my aluminum extrusions with a diffuser and they are very low profile, just as I like them. When the hardware runs I will try to put more effort into the gapless connector and look for mounting options for handles and the battery. There is the beauty on open source designs, as the way Martins MIW is constructed does not fit my very minimalistic approach, but might suit others. This way we can supply more options for cases, handles, etc. Just Beautiful.

dirkessl, 2020-12-20:
@DaveStu It works a breeze with the Arduino IDE, as Martin has ironed out all the issues with special libraries. I will provide an detailed instruction on how to install the Arduino IDE and the needed libraries shortly. We will also share an already compiled binary which can be flashed by an inexperienced user with a small tool. We can use the releases feature of github and share a nice changelog.

dirkessl, 2020-12-20:
Documentation is done for compiling it in the Arduino IDE https://github.com/MartinNohr/MagicImageWand/wiki/9.-Compiling-from-source

MartinNohr, 2020-12-21:
I got the BMP preview working nicely now. It's on the first menu. You can use the dial to scroll left and right by screens. It does have a bug for images less than 240 pixels wide. I'll fix that tomorrow, it's past midnight here and my brain goes foggy. :-)
Thanks for all the help guys. This is a great project.

MartinNohr, 2020-12-21:
Preview working fine on everything I tested. I'm sure you'll let me know of any problems. :-)
It's a neat feature.
Dirk: thanks again for the nice image samples. I especially like the space and the flame ones. I had created a simple wall of flame, that was the limit of my talent.

dirkessl, 2020-12-21:
Preview works fine, really amazing. Just I think scrolling is reversed on the wheel.

My physical build is done, everything works amazingly well. I have some minor issues with the hardware, but will sort them out for sure. I have not run the LEDs on full brightness, yet, but have never needed full brightness on my previous build. Timing on the ESP is much faster which is very nice and will help for sure in the future.

Martin, your talent to code this is out of this world, I am absolutely blown away by the features you have implemented. Truly stunning. I guess it can easily be extended to be of use for other projects, a VILTROX Weeylite RB08P could easily be made for much less money. The TTGO also has a Lipo charging circuit and this would make for a nice affordable RGB LED light. An SD reader is not needed and probably the inbuilt buttons would maybe be enough (but I admit the wheel is very nice) to drive very minimalistic menu system for hue, sat, and brightness + some inbuilt effects (they all have inbuilt effects these days like TV, Police, fire, etc.) A lot of hobby film makers are on a budget...

I will open issues for the bugs, I have found :-)

DaveStu, 2020-12-21:
@MartinNohr Sorry to hear about your loss, it's been an unprecedented year and much sadness. I've had a few friends and ex collegues go through the covid illness, and with some friends of friendswho have been taken away.
Plus UK has got one of the most inept governments in power right now, they've ruined brexit and handled covid so disastrously.

Your fresh foods gardening sounds wonderful, to have the ability. The most I've got to ability to grow are tomatoes and some herbs. The taste experience is very different indeed, comapred to commercial grown produce.
I used to have a friend in Tampa, who bring us florida oranges and admittedly the best oranges I've ever tasted.

DaveStu, 2020-12-21:
@dirkessl Thanks for the uploads.

Now that I've temporarily connected the parts (haven't got a breadboard), I'll compile/upload the code and give it a test run.
I've been running it through many test programs from various blogs. Had fun playing with all manner of light sequences, testing WIFI which works finding signals, also testing the display but now to some serious stuff.

Look what I found, though not what we need, just found it fascinating. The world of programmable RGB LED's is truly amazing.
https://www.twinkly.com/whats-new/
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
MartinNohr, 2020-12-26:
I put up new code this afternoon. I found a font that I think is much better. I had to shorten some of the menu lines, but it is much easier to read. I also added a system setting to change the menu colors. I'm not completely satisfied with how it works, so I will probably change it later when I think of a better way.

MartinNohr, 2020-12-26:
I added the IP address to the main menu so you can find it.
Dirk: Do you mind if I make some changes to the wifi code? I like what you have done so far, but it does need a bit more work. I see the uploading isn't working yet. It would also be nice to be able to get a list of the files down to the web browser. I think this is going to be much better than using Bluetooth. Thanks for your work on this, it's a great start.
I think I'd like to see the settings and be able to change things from the computer/phone web browser. This is going to stretch my knowledge of HTML and buttons and things that I have only a passing familiarity with.

dirkessl, 2020-12-26:
It was a very strange Christmas, indeed. We have a lockdown here in Germany so we are not allowed to be outside between 21:00 and 5:00. The kids were with us and we had a nice evening, but it was strange sending them home at 20:30. If you are outside at night without any urgent reason the police fines you at least EURO 500. My parents in law picked up food and presents from our doorstep as you can only celebrate with one other household so it was really strange not celebrating with them.

dirkessl, 2020-12-26:
@MartinNohr yes please change the code, as I am not very good in programming these advanced features. If you just put basic html code there, I can make it look prettier and responsive if you wish.

I am also thinking about the remote functionality, on how to implement this in a clever way. I guess we have two options here. We can either send commands to a remote unit with a webrequest when a pattern/image runs to a fixed address like http://192.168.4.100/remotestart and http://192.168.4.100/remotestop or we offer an URL which gets pulled by the receiver (http://192.168.4.1/isrunning), but I guess this will harder as the remote receiver needs to constantly pull the website of the MIW which might generate too much load or cause stutter on the MIW. I think I would prefer the first way. The receiving unit could then have a status LED which shows if the unit has received the command or it could use the display if we use another TTGO-Display or the other Board I found with the antenna connector.

MartinNohr, 2020-12-27:
We'll have to do a little experimenting to determine how much load we can put on it. It is a dual processor and pretty fast. Running the leds doesn't use too much computer time. What I don't know is if both of those processors are actually used when we compile single thread stuff. We might have to start using FREERTOS! I'm sure it supports both processors for tasks. It would be fun to have a real OS to work on again. Anyway, just thinking out loud.
It must be strangely quiet in the evening and night there. Almost no traffic, right?

MartinNohr, 2020-12-27:
I noted in the WiFi comments, but I'll mention it here also. I fixed the file upload to SD using WiFi.

MartinNohr, 2020-12-28:
I added a little feature. Pressing button 0 (on the board) will always display the image no matter what else is on the screen. Pressing it again restores whatever was going on before. Note that it doesn't work if an image is actually being shown on the LED strip of course.
I suppose we could make button 0 do other things, but I got tired of selecting a menu item to preview the file.

MartinNohr, 2020-12-28:
Dirk: Would you consider adding the sources for the STL files? Some people might need to modify them slightly for different extrusions.

dirkessl, 2020-12-28:
@MartinNohr sure, but as I use TinkerCAD for all of this, I can only supply online links. I guess I need to learn some Fusion360, I already have a license for it and think I will be much faster once I mastered it.

dirkessl, 2020-12-30:
Quick Update, I took the time today and learned Fusion 360 and created the basic case. I need to print one first, before I can make more adjustments, as I guess I did not include enough tolerances for 3D printing. But it is a good start and Fusion is really powerful.

DaveStu, 2020-12-31:
Morning/Evening
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

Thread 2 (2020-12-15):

gapless connector

dirkessl, 2020-12-15:
Design a connector that doesnt leave a gap and therefore a black line if joining 2 144 LED strips

DaveStu, 2021-11-16:
Hi Dirk, Hope you're well, its been a long while. Any change I can see your gplaess connector please. I've just started back on this project after being shelved for over a year, covid has changed history/life so much. Anyway, I've been trying to figure the option 2 method in martins options to arrange led strips differently to eliminate the gap, unfortunately I cannot get it to work. One strip works, the other doesnt in option 2. I'm also somewhat confused in the wiring the other strip, as it can only be powered in one direction. So, now back to original method, but trying to elimate black space again.

DaveStu, 2021-11-16:
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

I havent gone down the 3d printed route, after some investigating for a metal off the shelf setup I found a double flash bracket that worked and perfectly holds the alu profile. I mounted a third flash holder in the middle, then screwed in a multi-angle umbrella light stand bracket.
As the aluminium profile is light weight, this bracket holds them easily and tightly. I Now need to figure out the box for controller and battery, plus wiring. I'm finally getting somewhere.

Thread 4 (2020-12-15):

inbuilt remote for camera

dirkessl, 2020-12-15:
Idea:

Press start on the controller
controller sends signal to receiving unit, triggering bulb mode (or set timer on camera)
controller plays pixels
controller sends signal to receiving unit to close shutter

Either 433 Mhz with a module like this: https://www.aliexpress.com/item/32416047991.html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,searchweb201602_,searchweb201603_

or maybe BLE if range is enough.

highend: LoRa

MartinNohr, 2020-12-15:
This is a wonderful Idea! I like it.
I find that BLE will often go about 10m, but I think that is beyond what the spec says.

MartinNohr, 2020-12-15:
I have also found in testing that the WiFi radio will go closer to 30 meters outside. Maybe even further if the receiver is good.
I designed a radio controlled elevator button and I found it would easily go that far. I put an antenna on the receiver and it worked great, I don't know the exact distance because I didn't want to walk any further away from the house.
So we can probably use the WiFi on the TTGO and design a receiver for the camera. We might need to research how to actually trigger the camera but I hope that information is available somewhere.

dirkessl, 2020-12-15:
triggering the camera is easy with an arduino a resistor, and an 2N2222 transistor. I have built a camera timer based on the M5Stack, the schematics can be found at https://www.essl.de/2020/10/23/timy-the-open-source-camera-timer/ it would be a great addition to it, as the M5 already has WiFi. cheaper would of course be an additional TTGO.

dirkessl, 2020-12-16:
a candidate board for the reciever (or even for MIW): https://de.aliexpress.com/item/10000327309127.html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,searchweb201602_,searchweb201603_

as it has an ipex connector for an antenna

zhaoyu3517, 2021-05-09:
I use two esp8266 made a Wireless remote for camera.
use the esp-now:https://www.espressif.com/en/products/software/esp-now/overview
if i play the bmp,then the shutter will be pressed at the same time.

You can understand the principle by watching these videos
https://www.youtube.com/watch?v=w4R9VoY96h8
https://www.youtube.com/watch?v=qxwXwNS3Avw
https://www.youtube.com/watch?v=_cNAsTB5JpM

metalmaslow, 2021-07-28:
i love this  idea!

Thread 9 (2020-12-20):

Breadboard testing

MartinNohr, 2020-12-20:
If you are testing this on a breadboard make sure to lower the LED brightness. The power draw with lots of white lights can easily cause a voltage drop and the TTGO will freeze. Or you could also connect a separate power supply to the battery lines on the LED strip. I had a lot of crashes when just using the USB to power everything.
You could just set the brightness lower and then save the system settings with automatic load on.

dirkessl, 2020-12-28:
Interestingly, Is till run everything from the USB-C port and didn't have an issue, yet. I guess it depends on the LED strip, as they are all of mediocre quality. I have the power lines already soldered in, but as I am testing it is just easier to run it from the USB-C connector.

MartinNohr, 2021-01-31:
Well, mediocre quality perhaps, but to be fair, using the strips directly from a 3.3 V control line is out of spec. That isn't the problem I was seeing, but I have seen flickering lights on one strip until I used a logic level translator.

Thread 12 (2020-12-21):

when using inbuilt effects bmp preview is still shown

dirkessl, 2020-12-21:
not a big deal, but people might expect a preview of the effect which is of course hard to do.

MartinNohr, 2020-12-22:
I'll block it for the builtins. I couldn't think of a good way to show the builtins on the display. It might be possible though, I'll ponder it after I fix a few of the other issues. The main issue is how to handle the timing. The BMP files are static images while the builtins are mostly dynamic, they change in time. Perhaps I could just show the first 240 frames? It would be useful, you can't tell what they look like by displaying them until you take a picture of them.

MartinNohr, 2020-12-22:
Also let me know if you have any good ideas for more builtins.

MartinNohr, 2020-12-22:
eingebaut, (danish inbyggede), but the real english is reversed: built-in, not inbuilt :-)

MartinNohr, 2020-12-22:
I fixed this. This shows how elegant my menu system is (well, at least in my opinion). I just had to move one line in front of the eEndif instead of after it.
    {eIfEqual,false,"",NULL,&bShowBuiltInTests,true},
        {eBool,false,"Switch to SD Card",ToggleFilesBuiltin,&bShowBuiltInTests,0,0,0,"On","Off"},
    {eElse},
        {eBool,false,"Switch to Built-ins",ToggleFilesBuiltin,&bShowBuiltInTests,0,0,0,"On","Off"},
        {eText,false,"Preview BMP",ShowBmp},
    {eEndif},

Closed 2020-12-22.

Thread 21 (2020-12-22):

WiFi Image upload

dirkessl, 2020-12-22:
when in the field without a computer/SD reader it could be helpful to upload images over WiFi. Images can be converted with the online converter beforehand.
Care must be taken to not collide with the planned remote shutter functionality.
Idea: MIW will create a Hotspot and will offer a small website for uploading images and expose an API where the remote shutter can connect to. This will be a bit more work on the remote shutter, as it needs an UI to connect to the MIW

dirkessl, 2020-12-22:
I have started on the WiFi code, testing if it compiles. It seems with BLE enabled it did not work as the WiFi module was suing the same dram space. Now with BLE removed it creates an AP which you can connect to. Removing BLE also brought back a lot of program storage space.

MartinNohr, 2020-12-23:
BLE is a memory hog, mostly because I think it includes all of bluetooth classic. I'm surprised you can't use both, but I never tried that.

MartinNohr, 2020-12-23:
I'm not sure BLE is very useful, but wifi is probably extremely useful.
My wifi skills are weak, I appreciate greatly the work you do on this. Thanks.

dirkessl, 2020-12-23:
I am having a hard time implementing it :-) I will try further after the Christmas

dirkessl, 2020-12-25:
@MartinNohr I have implemented preliminary WiFi functions, I just can't get the upload / download stuff not to work If you could have a look into those functions, that would be awesome. I also don't know where the uploaded files should go to, maybe into an additional wifi folder? I am sure you have some ideas on this.

MartinNohr, 2020-12-26:
I'm done with other stuff for now so I will take a look at this soon.
BTW, I notice you're using F("..."). It doesn't hurt anything but it isn't necessary on the ESP32. The old arduinos had 2k of ram, esp32 has 520k built-in and usually 4M external. There's plenty of memory now.
You might have done some work on the download already, I just tried it and it worked, the only problem (at least with Android) is that .phps extension gets appended to the filename and has to be removed in order to use the file normally.
Uploading files doesn't work, I'll fix the .open call. I wish the SD library worked like standard C file IO, but it doesn't work the same, similar but not exact. I found a library to implement standard C file IO calls on the esp32 but I haven't found all the pieces to make it work yet. Future project.
There should also be a function to get the SD file list back to the web browser so the user can see what files are on the SD card.

MartinNohr, 2020-12-27:
I fixed the file upload. You can now upload files. It does need some improvements, like handling a filename that already exists.
We also need the ability to show a list of existing files on the SD card. I'll see if I can figure out how to do that.

MartinNohr, 2020-12-27:
Other features:
- show a list of existing file, maybe from a button press.
- show settings and allow starting playback.

MartinNohr, 2020-12-27:
I figured out how to show a list of the files on the download page, but I don't know enough HTML to figure out how to make them clickable for selection.

MartinNohr, 2020-12-27:
I added a couple of settings on a new page. Not very fancy, I need to learn a lot more about HTML. Like, how to change those settings, and a prettier display.

dirkessl, 2020-12-27:
Nice work, I tried the upload function and it works, but the uploaded picture does not show on the MIW. Filename when uploaded from iOS is something like FDB159FC-2E4E-43EE-A48E-59C14864F147.bmb so that's very long and very practical. Maybe we should add another textfield to the upload function where one can type in a desired name. If no name is given, it reverts back to upload + random(100,99999)

I saw the new settings page, really great. how would you want to change the settings there? with up/down arrows? I could make the buttons and you provide the code for changing the values. A simple text field would of course also work.

MartinNohr, 2020-12-28:
I forgot to reload the file list. If you reboot, or change folders and then come back the file will appear.

MartinNohr, 2020-12-28:
There are many more settings to implement. We should consider how to organize them so we don't make a complicated mess. Perhaps something along the same organization as the menus on the Wand would be good. Spin buttons would be nice but manual entry is acceptable to me.
I've been reading about how html works. I'm slowly starting to understand.
I think I might even know how to make the filenames selectable from the list, and to change folders!
We should be careful at this point that we don't start working in the same areas of the HTML code, we might have a lot of conflict resolution to do when we check in changes!
If you could code a sample spinner button for the column time I can probably figure out the others.
Some of the settings are also check boxes.
Supper time here, must go eat!

dirkessl, 2020-12-28:
> I forgot to reload the file list. If you reboot, or change folders and then come back the file will appear.

Martin, try yourself: rename a bmp to FDB159FC-2E4E-43EE-A48E-59C14864F147.bmb and it wont show up in the list.

MartinNohr, 2021-01-18:
Interesting. I'll look at that as soon as I can. I teach a digital photography class at the university here, and I need to finish my lecture notes for tomorrows first class. Sorry I just noticed now, so late.
BTW, there were some problems with long names that I fixed, so this might have gone away already.

MartinNohr, 2021-01-22:
There was a 39 character filename length limit in the code. I changed it to 99. Your long name works fine now.

MartinNohr, 2022-09-18:
I have fixed many of the above issues with upload/download. The settings page now allows text entry to change various settings. I don't think we need to have all of them, but it could be done. The code is list driven so we can add whatever controls we want to show up on the web settings page without typing a lot of HTML. It doesn't have menu levels like the MIW, just titles between sections. Values are all shown as text or checkboxes. I suppose spin buttons might be useful, so might sliders also. I'll think about that later.
Up and downloading files is much better now, the only missing thing is the ability to select the upload folder, it always puts them in the root. I will change that when I have some more time. I've learned enough HTML to do some of these things
Try the latest version and let me know what you think.

MartinNohr, 2022-10-04:
I've now improved the server pages a lot. What do you think?

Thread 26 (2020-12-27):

MIW Remote control esp pin input only, won't work

MartinNohr, 2020-12-27:
Pins 34-39 on esp32 are input only, they cannot be used for output control. I suggest pin 21, 22, 32, or 33. Although any of the other outputs could be used, there isn't any conflict since they aren't being used. But leaving the SD pins free means we could add an SD card if necessary in the future.
Please change the schematic.

dirkessl, 2020-12-28:
Fixed

Closed 2020-12-28.

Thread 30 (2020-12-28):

Preview on folder gives error message and then previews gives out of memory later

MartinNohr, 2020-12-28:
If the currently selected file is really a folder and the preview button is pressed there will be an error message that the file can't be opened. Unfortunately the screen buffer was already allocated and the memory never released. If a valid file is then selected the preview will fail with a not enough memory error.

MartinNohr, 2020-12-29:
Fixed. Call to free() was missing and folders shouldn't be selected. Both issues fixed.

Closed 2020-12-29.

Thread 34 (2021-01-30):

Control of the stripes

firefighter2608, 2021-01-30:
I would like to push the two stirpes completely together in the middle and start the lines for the stripes once from above and the other from below. then I have no gap in the middle. can ma set this in the code so that it rotates the control by 180 degrees or something like that?
I would appreciate an answer.
Thanks in advance
Peter

MartinNohr, 2021-01-31:
Should be possible of course. I'm busy for the next couple of days, but I will take a look at it as soon as I can. Thanks for the suggestion. You're talking about the built-in stripes pattern, correct?

firefighter2608, 2021-01-31:
Super thank you.
yes it's about the black stripe between the upper and lower stripe. Then you could connect them without a gap and then control them from above and below.

MartinNohr, 2021-01-31:
Can you draw me a picture of what it would look like to make sure I understand correctly?
Thx

firefighter2608, 2021-02-02:
I hope the drawing is understandable.
My idea would be to reverse the LED control in the software, change from current LED1 to LED144. this for every stripe, then you could connect the stripes without a gap but electrically separated and the black line would be gone.

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

MartinNohr, 2021-02-03:
Aha, I misunderstood at first, now I see what you are trying to do. I originally did that, but I didn't like running the wires down to the ends of the strip. However, if you don't care about that then this is easily done. Here's the code that handles it.
This would need to be changed so that they are reversed. I can change it for you but it will be a couple of days before I get around to it. In any case, the mapping is all handled in this one routine which should make it easy to change.
int AdjustStripIndex(int ix)
{
	if (ix < NUM_LEDS) {
		ix = (NUM_LEDS - 1 - ix);
	}
	ix = max(0, ix);
	ix = min(STRIPLENGTH - 1, ix);
	return ix;
}
This just needs to be changed to reverse the mapping to each strip.
I think... I'll consider it later this week when I have some more time to think about this carefully. But I think it will be easy to change.

MartinNohr, 2021-02-03:
Actually, this might do it...
int AdjustStripIndex(int ix)
{
	if (ix >= NUM_LEDS) {
		ix = (NUM_LEDS - 1 - ix);
	}
	ix = max(0, ix);
	ix = min(STRIPLENGTH - 1, ix);
	return ix;
}

MartinNohr, 2021-02-03:
I think the above will work, all you do is change the < to >=. I'll test it later this week if you don't have time to test it. I think it will work, but sometimes I make mistakes. :-)

MartinNohr, 2021-02-03:
BTW, I think you have a really good idea. Without those wires you can easily mash the led's close together and get rid of the black stripe down the middle. I designed a clip to hold the wires to the aluminum extrusion, but I didn't like having that wire running down to the end. But maybe having that is ok given that the black stripe disappears. Next time I work on the software I might add this as an option so it will be easy to change for either wiring method.
Thanks for the idea. I appreciate it when people suggest good ideas. I never think of everything.

firefighter2608, 2021-02-03:
great, thank you very much for the work. the stick works great. is already my third project which I am recreating, but this one is really perfect. Thanks a lot for this. i will test it on the weekend. the wires can be hidden in my profile on the sides. I will report it.

MartinNohr, 2021-02-04:
I'm going to put a new option in the code. I think there are three possible connections that make sense.
1. Both data inputs in the middle.
2. Both data inputs on the outside. (your idea)
3. Data input for stick 1 on the bottom, and the output from 1 connected to the input of 2, set the number of pixels to 288.
I'll add this option to the menu in the next couple of days.

firefighter2608, 2021-02-04:
I'm going to put a new option in the code. I think there are three possible connections that make sense.

Both data inputs in the middle.
Both data inputs on the outside. (your idea)
Data input for stick 1 on the bottom, and the output from 1 connected to the input of 2, set the number of pixels to 288.
I'll add this option to the menu in the next couple of days.

MartinNohr, 2021-02-05:
Looks like you quoted me, was there a comment also? I'm not seeing it.

ThomasKlee64, 2021-05-29:
Hello Martin,

i have a problem with the second LED Stripe, this one unfortunately does not work. I have selected in the menu under LED Strip Settings Total LED 288 and under LED wiring Mode 2. Unfortunately the second stripe is dead. Both LED strips are connected to the data pin input, is that correct?

What could I have done wrong here?

THX

Thomas

MartinNohr, 2021-06-05:
The code now has code for the three different wiring options. It is working, I'll close this now.

MartinNohr, 2021-07-08:
I just noticed this while cleaning my email. If I never answered… sorry.
Is this still a problem, or did you figure it out?
There are two data “output” pins. One for each strip.
Are you using my PCB, or did you make your own circuit?
If you respond to ***@***.*** I will probably respond faster! This email is getting too much spam.
Martin

Sent from Mail for Windows 10

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

Closed 2021-06-05.

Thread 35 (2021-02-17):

M5 Core2 Port

MartinNohr, 2021-02-17:
It would be interesting and useful to port the code to run on the M5 Core2 system.

_Originally posted by @MartinNohr in https://github.com/MartinNohr/MagicImageWand/issues/1#issuecomment-770267243_

MartinNohr, 2021-02-17:
I have an M5 Core2 now. I'll port the code as soon as I have some free time.

MartinNohr, 2021-03-25:
I almost have the port to the M5 working. I'll create a new github entry for it as soon as I'm satisfied. It was a bit of work, the screen is different and I decided to enable touch detection. The touch detection isn't great, the screen is small, but it does work. It might be good to still use the dial, it is in many ways easier to use, especially with gloves one.
I'm thinking of using the level sensor on the M5 to show if you're holding the wand level! I might even use it so you can shake the wand to start it playing.

MartinNohr, 2021-04-18:
I'm not finding the touch screen on the core2 to be very reliable or useful. So I have ported the code to the original M5Stack with 3 physical buttons. This is proving to be quite good. I'll post the code when enough of it is working and put a link here.

dirkessl, 2021-05-27:
That is awesome news, it would make it possible to make a MIW without any soldering (when skipping the rotary dial) as it has enough connectors free to plug the LED strip and the rotary dial, making it very easy for even more people building one. I have the older version without the touchscreen and use it as a timer and absolutely love it.

MartinNohr, 2021-06-02:
https://github.com/MartinNohr/MagicImageWand-M5Stack/tree/master
Macros aren't working yet, and the calibration for the level sensor is hard-coded.
Please try the code.
There is some soldering, but not much. The display is beautiful.
I'll add some pictures of the wiring harness that I made.

MartinNohr, 2021-06-02:
I haven't put the rotary dial in yet. Also, I think the M5 SD code only handles <=32G cards.

MartinNohr, 2021-06-05:
I made a mistake. The link I sent you above was for the M5 Stack new version with the touch screen. I didn't like it and never finished it.
Here is the one for the original M5 Stack with the 3 buttons. It is the grey version, but might work on the white one also.
https://github.com/MartinNohr/MagicImageWand-M5StackGray

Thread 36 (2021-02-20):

A few errors....

krealab, 2021-02-20:
Hi! I just ordered the TTGO board and downloaded the code. Followed the instructions in the wiki, but ending up with a few errors..... :

Arduino:1.8.13 (Mac OS X), Kort"ESP32 Dev Module, Disabled, Default 4MB with spiffs (1.2MB APP/1.5MB SPIFFS), 240MHz (WiFi/BT), QIO, 80MHz, 4MB (32Mb), 921600, None"

In file included from sketch/MagicImageWand.h:52:0,
                 from /Users/kolbjorn/Dropbox/Min Mac (Kolbjørns MacBook Pro)/Desktop/MagicImageWand/MagicImageWand.ino:7:
/Users/kolbjorn/Dropbox/Min Mac (Kolbjørns MacBook Pro)/Documents/Arduino/libraries/FastLED/src/FastLED.h:14:21: note: #pragma message: FastLED version 3.004.000
 #    pragma message "FastLED version 3.004.000"
                     ^
In file included from /Users/kolbjorn/Dropbox/Min Mac (Kolbjørns MacBook Pro)/Documents/Arduino/libraries/FastLED/src/FastLED.h:65:0,
                 from sketch/MagicImageWand.h:52,
                 from /Users/kolbjorn/Dropbox/Min Mac (Kolbjørns MacBook Pro)/Desktop/MagicImageWand/MagicImageWand.ino:7:
/Users/kolbjorn/Dropbox/Min Mac (Kolbjørns MacBook Pro)/Documents/Arduino/libraries/FastLED/src/fastspi.h:135:23: note: #pragma message: No hardware SPI pins defined.  All SPI access will default to bitbanged output
 #      pragma message "No hardware SPI pins defined.  All SPI access will default to bitbanged output"
                       ^
Traceback (most recent call last):
  File "esptool.py", line 57, in <module>
  File "/Library/Python/2.7/site-packages/PyInstaller/loader/pyimod03_importers.py", line 389, in load_module
  File "serial/tools/list_ports.py", line 29, in <module>
  File "/Library/Python/2.7/site-packages/PyInstaller/loader/pyimod03_importers.py", line 389, in load_module
  File "serial/tools/list_ports_posix.py", line 31, in <module>
  File "/Library/Python/2.7/site-packages/PyInstaller/loader/pyimod03_importers.py", line 389, in load_module
  File "serial/tools/list_ports_osx.py", line 32, in <module>
ValueError: dlsym(RTLD_DEFAULT, kIOMasterPortDefault): symbol not found
Failed to execute script esptool
Mange bibliotek ble funnet for "FastLED.h"
I bruk: /Users/kolbjorn/Dropbox/Min Mac (Kolbjørns MacBook Pro)/Documents/Arduino/libraries/FastLED
Ikke i bruk: /Users/kolbjorn/Dropbox/Min Mac (Kolbjørns MacBook Pro)/Documents/Arduino/libraries/FastLED-master
Mange bibliotek ble funnet for "WiFi.h"
I bruk: /Users/kolbjorn/Library/Arduino15/packages/esp32/hardware/esp32/1.0.4/libraries/WiFi
Ikke i bruk: /Applications/Arduino.app/Contents/Java/libraries/WiFi
exit status 255
/Applications/Arduino.app/Contents/Java/arduino-builder returnerte 255
Feil ved kompilering for kort ESP32 Dev Module.

dirkessl, 2021-02-20:
Have you done all steps as in https://github.com/MartinNohr/MagicImageWand/wiki/9.-Compiling-from-source
?

krealab, 2021-02-21:
Yes. I really dont know what the problem is. But i will try a different computer on windows. This i tried on a Mac. This error keeps popping up: enumeration value 'eIfEqual' not handled in switch [-Werror=switch]

Kolbjørn

MartinNohr, 2021-02-22:
First, ignore the pragma messages, they do not indicate a problem. They are just information.
I'm not sure what the Mac messages mean, but I can read the norwegian. It appears among other things that it is finding more than one version of the fastled.h library. Interesting. Are you using arduino IDE? Have you set the correct TTGO device?
The 'eIfEqual' is defined as an enum in the .h file. I do not know why that would cause a compile error. It is a constant value used in a switch in the code, but other constants are also used in switch statements. I have a Mac here, but I have never used it to compile Arduino code.

krealab, 2021-02-23:
I did the same process on a windows computer. It all works now. So now i need the hardware. Do you sell it or should i get it from Amazon? Kolbjørn

MartinNohr, 2021-02-24:
Which hardware? There are lots of parts! The led strips are available from Amazon or banggood. I think I listed them in the docx file.
You can build your own ttgo connections but it you like the PCB version, it is available from me. I have designed a new version of the 3D case, but I haven't uploaded it yet. The PCB has a socket for the TTGO chip and all the components including the rotary switch are soldered on. I can sell the PCB for $20 without the TTGO chip. You'll have to pay some shipping of course.

MartinNohr, 2021-02-24:
Here are photos of the PCB.
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

MartinNohr, 2021-02-24:
There is a newer design with some minor changes that you will be able to order directly from PCBWAY.com in China. It is about a month away from being finalized. I'll post the link when I have tested the prototypes.

ahennies-22, 2021-04-14:
Is there still a possibility to get an assembled board? If not, is there already news about the new board?

MartinNohr, 2021-04-14:
Yes, I have 16 PCB's available. $35 + shipping. This includes a programmed TTGO. I just need an address and I can get the shipping cost.
You will be able to get the board from PCBWAY.com without the TTGO. It will be available soon. I'll send the link when it is ready.

ahennies-22, 2021-04-14:
@MartinNohr
Hallo,
die Anschrift lautet:
Achim Hennies
Klappenbergweg 14
37176 Nörten-Hardenberg
Kann ich vielleicht per PayPal Freunde bezahlen?
Schöne Grüße
Achim ahennies-22

MartinNohr, 2021-04-14:
martinnohr76@gmail.com
Let me know when you send an email. I don't want to leave this email public for very long. I'll delete it after you have it.

ahennies-22, 2021-04-14:
You can delete it

MartinNohr, 2021-04-29:
> Yes. I really dont know what the problem is. But i will try a different computer on windows. This i tried on a Mac. This error keeps popping up: enumeration value 'eIfEqual' not handled in switch [-Werror=switch]
>
> Kolbjørn

I think I may have solved this compile problem in the latest version of the code. Some compilers issue a warning/error if all of the enums are not handled in a switch statement. This is perhaps a good idea since it will warn you about missing case statements. Please try compiling it on the system that gave the error and let me know. Thanks.

ahennies-22, 2021-04-29:
I am very sorry, but I still get this known error message. For more details
I have put the output of the compilation into a file. I hope it helps.
The compile process stops in line 334.
Achim

Am Do., 29. Apr. 2021 um 16:28 Uhr schrieb MartinNohr <
***@***.***>:

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

Arduino: 1.8.13 (Windows 10), Board: "ESP32 Dev Module, Disabled, Default 4MB with spiffs (1.2MB APP/1.5MB SPIFFS), 240MHz (WiFi/BT), QIO, 80MHz, 4MB (32Mb), 921600, None"

In file included from C:\Users\hennies\Documents\Arduino\libraries\TFT_eSPI/User_Setup_Select.h:133:0,

                 from C:\Users\hennies\Documents\Arduino\libraries\TFT_eSPI/TFT_eSPI.h:39,

                 from sketch\MagicImageWand.h:61,

                 from D:\Pixelstick\MagicImageWand\MagicImageWand.ino:7:

C:\Users\hennies\Documents\Arduino\libraries\TFT_eSPI/TFT_Drivers/ILI9341_Defines.h:4:0: warning: "TFT_HEIGHT" redefined

 #define TFT_HEIGHT 320

 ^

In file included from C:\Users\hennies\Documents\Arduino\libraries\TFT_eSPI/User_Setup_Select.h:22:0,

                 from C:\Users\hennies\Documents\Arduino\libraries\TFT_eSPI/TFT_eSPI.h:39,

                 from sketch\MagicImageWand.h:61,

                 from D:\Pixelstick\MagicImageWand\MagicImageWand.ino:7:

C:\Users\hennies\Documents\Arduino\libraries\TFT_eSPI/User_Setup.h:83:0: note: this is the location of the previous definition

 #define TFT_HEIGHT 240 // GC9A01 240 x 240

 ^

In file included from C:\Users\hennies\Documents\Arduino\libraries\TFT_eSPI/Processors/TFT_eSPI_ESP32.h:78:0,

                 from C:\Users\hennies\Documents\Arduino\libraries\TFT_eSPI/TFT_eSPI.h:52,

                 from sketch\MagicImageWand.h:61,

                 from D:\Pixelstick\MagicImageWand\MagicImageWand.ino:7:

C:\Users\hennies\AppData\Local\Arduino15\packages\esp32\hardware\esp32\1.0.6\libraries\FS\src/FS.h:30:0: warning: "FILE_READ" redefined

 #define FILE_READ       "r"

 ^

In file included from C:\Users\hennies\Documents\Arduino\libraries\SdFat\src/ExFatLib/ExFatFile.h:797:0,

                 from C:\Users\hennies\Documents\Arduino\libraries\SdFat\src/ExFatLib/ExFatVolume.h:28,

                 from C:\Users\hennies\Documents\Arduino\libraries\SdFat\src/ExFatLib/ExFatLib.h:27,

                 from C:\Users\hennies\Documents\Arduino\libraries\SdFat\src/sdfat.h:33,

                 from sketch\MagicImageWand.h:34,

                 from D:\Pixelstick\MagicImageWand\MagicImageWand.ino:7:

c:\users\hennies\documents\arduino\libraries\sdfat\src\common\arduinofiles.h:31:0: note: this is the location of the previous definition

 #define FILE_READ O_RDONLY

 ^

In file included from C:\Users\hennies\Documents\Arduino\libraries\TFT_eSPI/Processors/TFT_eSPI_ESP32.h:78:0,

                 from C:\Users\hennies\Documents\Arduino\libraries\TFT_eSPI/TFT_eSPI.h:52,

                 from sketch\MagicImageWand.h:61,

                 from D:\Pixelstick\MagicImageWand\MagicImageWand.ino:7:

C:\Users\hennies\AppData\Local\Arduino15\packages\esp32\hardware\esp32\1.0.6\libraries\FS\src/FS.h:31:0: warning: "FILE_WRITE" redefined

 #define FILE_WRITE      "w"

 ^

In file included from C:\Users\hennies\Documents\Arduino\libraries\SdFat\src/ExFatLib/ExFatFile.h:797:0,

                 from C:\Users\hennies\Documents\Arduino\libraries\SdFat\src/ExFatLib/ExFatVolume.h:28,

                 from C:\Users\hennies\Documents\Arduino\libraries\SdFat\src/ExFatLib/ExFatLib.h:27,

                 from C:\Users\hennies\Documents\Arduino\libraries\SdFat\src/sdfat.h:33,

                 from sketch\MagicImageWand.h:34,

                 from D:\Pixelstick\MagicImageWand\MagicImageWand.ino:7:

c:\users\hennies\documents\arduino\libraries\sdfat\src\common\arduinofiles.h:35:0: note: this is the location of the previous definition

 #define FILE_WRITE (O_RDWR | O_CREAT | O_AT_END)

 ^

D:\Pixelstick\MagicImageWand\MagicImageWand.ino:3006:11: warning: multi-character character constant [-Wmultichar]

   a1[0] = '0x7e';

           ^

D:\Pixelstick\MagicImageWand\MagicImageWand.ino:3008:11: warning: multi-character character constant [-Wmultichar]

   b1[0] = '0x7e';

           ^

In file included from sketch\MagicImageWand.h:58:0,

                 from D:\Pixelstick\MagicImageWand\MagicImageWand.ino:7:

C:\Users\hennies\Documents\Arduino\libraries\FastLED\src/FastLED.h:14:21: note: #pragma message: FastLED version 3.004.000

 #    pragma message "FastLED version 3.004.000"

                     ^

In file included from C:\Users\hennies\Documents\Arduino\libraries\FastLED\src/FastLED.h:65:0,

                 from sketch\MagicImageWand.h:58,

                 from D:\Pixelstick\MagicImageWand\MagicImageWand.ino:7:

C:\Users\hennies\Documents\Arduino\libraries\FastLED\src/fastspi.h:135:23: note: #pragma message: No hardware SPI pins defined.  All SPI access will default to bitbanged output

 #      pragma message "No hardware SPI pins defined.  All SPI access will default to bitbanged output"

                       ^

In file included from D:\Pixelstick\MagicImageWand\MagicImageWand.ino:7:0:

sketch\MagicImageWand.h:583:1: warning: ISO C++ forbids converting a string constant to 'char*' [-Wwrite-strings]

 };

 ^

sketch\MagicImageWand.h:583:1: warning: ISO C++ forbids converting a string constant to 'char*' [-Wwrite-strings]

sketch\MagicImageWand.h:594:1: warning: ISO C++ forbids converting a string constant to 'char*' [-Wwrite-strings]

 };

 ^

sketch\MagicImageWand.h:594:1: warning: ISO C++ forbids converting a string constant to 'char*' [-Wwrite-strings]

sketch\MagicImageWand.h:594:1: warning: ISO C++ forbids converting a string constant to 'char*' [-Wwrite-strings]

sketch\MagicImageWand.h:594:1: warning: ISO C++ forbids converting a string constant to 'char*' [-Wwrite-strings]
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

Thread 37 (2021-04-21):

I made two more

zhaoyu3517, 2021-04-21:
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

This use two 18350 battery. One 144 LED strips.
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

This use 4 18350 battery. Two 144 LED strips.

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

MartinNohr, 2021-06-05:
Very nice mechanical design. I am impressed.
I have added many improvements to the code, take a look when you have time.
One of the things I added is an option to display the battery voltage. I use two 18650 on mine and 20k/10k voltage divider to drop the battery voltage down to <3.3. With proper calibration you can then an approximate % battery.
I also added an option to control the maximum current that is allowed.
Many other changes in the last couple of weeks also.

MartinNohr, 2021-06-05:
The menus and filenames now automatically scroll sideways if they are too long for the screen.

MartinNohr, 2021-07-08:
You have inspired me to improve my own mechanical and electrical design. I modified the PCB so it now has a power supply on the PCB. This makes hooking things up much easier. It is only 2Amp but I have seldom needed even that much during night photography.
I have also added a light sensor, which could be used for remote IR triggering or to automatically control the brightness. I don't know if that is useful or not, I'm just experimenting. :-)
You have the best mechanical design I have seen, thanks for sharing the photos.

zhaoyu3517, 2021-07-15:
I saw your design, you do better. :D

metalmaslow, 2021-07-28:
wow looks awesome!

codenamekraken, 2024-12-19:
> I saw your design, you do better. :D

can you plese help me i also want to make this

codenamekraken, 2024-12-25:
> Very nice mechanical design. I am impressed. I have added many improvements to the code, take a look when you have time. One of the things I added is an option to display the battery voltage. I use two 18650 on mine and 20k/10k voltage divider to drop the battery voltage down to <3.3. With proper calibration you can then an approximate % battery. I also added an option to control the maximum current that is allowed. Many other changes in the last couple of weeks also.

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

  can you help budy

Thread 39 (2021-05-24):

Some questions about the new version with TTGO part

ThomasKlee64, 2021-05-24:
Hello Martin,

I came across this project with great interest and still have a few questions for me as a beginner!
I have read that there are already previous versions of the project, among other things with the ESP32 WIFIVERSION 2HELTEC KIT 32. Now a different device is used. I'm not quite clear from the schematic. Here the ESP32 TTGO device is operated without 3.3V?

[https://github.com/MartinNohr/MagicImageWand/blob/main/TTGO%20Magic%20Image%20Wand%20Schematic.pdf](url)

And what's the deal with the wiring diagram remote. I apologize for my perhaps stupid questions. If you could help me here the start in this project something I would be grateful.

[https://github.com/MartinNohr/MagicImageWand/blob/main/TTGO%20Magic%20Image%20Wand%20Remote.pdf](url)

THX

Thomas

zhaoyu3517, 2021-05-24:
TTGO display can use  5V. So you can input 5V or 3.3V or use lithium battery. But only one can be used, not at the same time.

ThomasKlee64, 2021-05-30:
Thanks for the answer

MartinNohr, 2021-08-13:
I'm not sure I answered this completely yet.
TTGO has its own 3.3 V regulator, so you can feed it with 5V and it works just fine. The 5V is necessary for the WS2812 LED strips so you have to have 5V around anyway. The data line to the LEDS seems to work with the 3.3V control lines, but it is out of spec, that is why I added level shifters to the PCB I designed. Of course the PCB also makes all the wiring easy since the rotary dial switch is on the PCB. My latest PCB even has a 5V regulator on the board. I created a new design that now uses a pair of 18650 batteries in the handle. Works much better and is much easier to build.
The remove schematic is for another device that is used to remotely trigger the camera. I haven't finished the software for that yet, but I will get it done eventually. It will automatically open the camera shutter when the wand display is started. You don't need an assistant or a remote control for the camera!

Closed 2021-05-30.

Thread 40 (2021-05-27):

missing source files

dirkessl, 2021-05-27:
SdFatConfig.h and nvs_flash.h are missing from the source files.

MartinNohr, 2021-06-02:
nvs_flash.h is part of the esp32 library. If it is missing try installing the latest board support. I do not want to add it to this github repository.
I don't understand why sdfatconfig.h would be missing. It has been required for a long time and has never been part of this github repository. It is part the sdfat library.

dirkessl, 2021-06-04:
This was me being stupid... I tried compiling it with VsCode, which has no libraries installed. Works with the Arduino IDE.

Closed 2021-06-02.

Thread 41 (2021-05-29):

Output 2 for the second LED stripe not work

ThomasKlee64, 2021-05-29:
Hello Martin,

i have a problem with the second LED Stripe, this one unfortunately does not work. I have selected in the menu under LED Strip Settings Total LED 288 and under LED wiring Mode 2. Unfortunately the second stripe is dead. Both LED strips are connected to the data pin input, is that correct?

What could I have done wrong here?

THX

Thomas

ThomasKlee64, 2021-05-29:
Sorry, had forgotten to set the number of LED controllers to 2.

MartinNohr, 2021-06-05:
Yep, that would certainly cause a problem! Glad you found it, it puzzled me.

Closed 2021-05-29.

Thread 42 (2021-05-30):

MagicImageWand with larger 3 or 4 inches Display

ThomasKlee64, 2021-05-30:
Hello Martin,

I have a question. I have rebuilt the MagicImageWand with a lot of friends and I am excited about it. I would like to try to build the whole thing with a larger TFT display 3 or 4 inches and an ESP32 NodeMCU Module WLAN WiFi Dev Kit C Development Board. Is it possible to adapt the code?

Many greetings

Thomas

MartinNohr, 2021-06-02:
Yes, but I am not sure how much work. If the display works with the tft_espi library it should be pretty easy to do. You will probably have to change some of the GPIO pins for the SD card and the rotary switch.
I am in the process of porting the code to the TTGO T4 which has a 2 1/4 inch display. It is supported by Bodmer's TFT library so it is very easy to do. The board also has an SD reader.

MartinNohr, 2021-06-05:
I reopened this as I am working on the TTGO T4 with a larger display. I'll post information here when it is ready.

ThomasKlee64, 2021-06-05:
Great news, am looking forward to the first results.

MartinNohr, 2021-07-08:
Coming soon on this project. I just had to get some other projects finished. Maybe by September I'll have the code working.

DaveStu, 2021-11-16:
Hi Martin, hope you're well. It's been a while my friend. I'm wondering as you're porting the code to a larger display board, does the current uploaded code uploaded still work with the  original TTGO?
I've tried compiling it and it breaks with 'gfxglyh does not name a type. in fonts.h

I'm wondering if this is the newer code for TTGO T4 or are they interchangeable as they use the same microcontroller?
Thanks

MartinNohr, 2021-11-17:
I haven't seen that error. I haven't ported the code to any larger display yet and I don't think I changed fonts.h. Weird.
It should still work with the original TTGO, that's what I'm using.

DaveStu, 2021-11-17:
Hey Martin, I did assume that as it it would have been documnted and/or new project started.
So, I did a refresh of the Arduino program (always a good starting point). Followed the guide, set it all up, added and updated libraries, the ''gfxglyh' error has gone, though now it breaks at 'Error compiling for board ESP32 Dev Module'.
Im using yout latest code V1.15.

I'm on Arduino 1.8.16 with latest esp32 library V2.01. Then I tried V.2.00, V1.06 and V1.04 (Shown on your screenshots) and have the same problem. Failing that, perhaps an older version of Arduino, but would'nt make any logical sense?

On a different realted problem. I still have code V1.04 installed on the board so have been testing that whilst I get other issue figured. As I want to use two strips, I was trying to follow your section on 'Led Wirining Mode' and want to use mode 2 to create a "no black gap".
Now from my basic understanding, the strips are still wired the same as nomal being directional, the strips themselves are turned around/reversed?
I thought I was right, as when I execute 'cylon eye' pattern, STRIP1 is now reversed, but STRIP2 does not light up.
After a short delay, the sequence returns to STRIP1, the delay being that STRIP2 should be lighting up.
Now, do I actually need to wire them differently? (I was slightly confused by document) or is their a bug in code V1.04?
Of course as per instructions, no electrical contact in the middle is made.

The Idea is, that I carry two strips in half in a case then connect them up on site, because they are long.

DaveStu, 2021-11-17:
My error log

In file included from D:\ARDUINO\MagicImageWand\MagicImageWand.h:34,
                 from D:\ARDUINO\MagicImageWand\MagicImageWand.ino:7:
C:\Users\SUPERMAN\Documents\Arduino\libraries\SdFat\src/sdfat.h:438:2: warning: #warning File not defined because __has__include(FS.h) [-Wcpp]
 #warning File not defined because __has__include(FS.h)
  ^~~~~~~
In file included from C:\Users\SUPERMAN\Documents\Arduino\libraries\FastLED\src/platforms/esp/32/clockless_rmt_esp32.h:116,
                 from C:\Users\SUPERMAN\Documents\Arduino\libraries\FastLED\src/platforms/esp/32/fastled_esp32.h:8,
                 from C:\Users\SUPERMAN\Documents\Arduino\libraries\FastLED\src/platforms.h:36,
                 from C:\Users\SUPERMAN\Documents\Arduino\libraries\FastLED\src/FastLED.h:52,
                 from D:\ARDUINO\MagicImageWand\MagicImageWand.h:58,
                 from D:\ARDUINO\MagicImageWand\MagicImageWand.ino:7:
C:\Users\SUPERMAN\AppData\Local\Arduino15\packages\esp32\hardware\esp32\2.0.1/tools/sdk/esp32/include/esp_hw_support/include/esp_intr.h:8:2: warning: #warning esp_intr.h is deprecated, please include esp_intr_alloc.h instead [-Wcpp]
 #warning esp_intr.h is deprecated, please include esp_intr_alloc.h instead
  ^~~~~~~
In file included from C:\Users\SUPERMAN\Documents\Arduino\libraries\TFT_eSPI/Processors/TFT_eSPI_ESP32.h:84,
                 from C:\Users\SUPERMAN\Documents\Arduino\libraries\TFT_eSPI/TFT_eSPI.h:65,
                 from D:\ARDUINO\MagicImageWand\MagicImageWand.h:61,
                 from D:\ARDUINO\MagicImageWand\MagicImageWand.ino:7:
C:\Users\SUPERMAN\AppData\Local\Arduino15\packages\esp32\hardware\esp32\2.0.1\libraries\FS\src/FS.h:30: warning: "FILE_READ" redefined
 #define FILE_READ       "r"

In file included from C:\Users\SUPERMAN\Documents\Arduino\libraries\SdFat\src/ExFatLib/ExFatFile.h:821,
                 from C:\Users\SUPERMAN\Documents\Arduino\libraries\SdFat\src/ExFatLib/ExFatVolume.h:27,
                 from C:\Users\SUPERMAN\Documents\Arduino\libraries\SdFat\src/ExFatLib/ExFatLib.h:27,
                 from C:\Users\SUPERMAN\Documents\Arduino\libraries\SdFat\src/sdfat.h:33,
                 from D:\ARDUINO\MagicImageWand\MagicImageWand.h:34,
                 from D:\ARDUINO\MagicImageWand\MagicImageWand.ino:7:
c:\users\superman\documents\arduino\libraries\sdfat\src\common\arduinofiles.h:31: note: this is the location of the previous definition
 #define FILE_READ O_RDONLY

In file included from C:\Users\SUPERMAN\Documents\Arduino\libraries\TFT_eSPI/Processors/TFT_eSPI_ESP32.h:84,
                 from C:\Users\SUPERMAN\Documents\Arduino\libraries\TFT_eSPI/TFT_eSPI.h:65,
                 from D:\ARDUINO\MagicImageWand\MagicImageWand.h:61,
                 from D:\ARDUINO\MagicImageWand\MagicImageWand.ino:7:
C:\Users\SUPERMAN\AppData\Local\Arduino15\packages\esp32\hardware\esp32\2.0.1\libraries\FS\src/FS.h:31: warning: "FILE_WRITE" redefined
 #define FILE_WRITE      "w"

In file included from C:\Users\SUPERMAN\Documents\Arduino\libraries\SdFat\src/ExFatLib/ExFatFile.h:821,
                 from C:\Users\SUPERMAN\Documents\Arduino\libraries\SdFat\src/ExFatLib/ExFatVolume.h:27,
                 from C:\Users\SUPERMAN\Documents\Arduino\libraries\SdFat\src/ExFatLib/ExFatLib.h:27,
                 from C:\Users\SUPERMAN\Documents\Arduino\libraries\SdFat\src/sdfat.h:33,
                 from D:\ARDUINO\MagicImageWand\MagicImageWand.h:34,
                 from D:\ARDUINO\MagicImageWand\MagicImageWand.ino:7:
c:\users\superman\documents\arduino\libraries\sdfat\src\common\arduinofiles.h:35: note: this is the location of the previous definition
 #define FILE_WRITE (O_RDWR | O_CREAT | O_AT_END)
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

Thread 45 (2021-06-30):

What is the function of the inputs for the frame sensor and the light sensor?

ThomasKlee64, 2021-06-30:
Hello, i have a question. What is the function of the inputs for the frame sensor and the light sensor? What can be done with this?

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

THX

Thomas

MartinNohr, 2021-07-08:
The frame sensor is for a wheel with an encoder that you attach to the bottom of the wand. You can roll it and it will advance the image to the next frame after every N pulses. This make for very accurate image creation without having to watch how fast you're walking. Unfortunately I haven't finished the design of the wheel/encoder yet. The code is working though, I have tested it.
The Light Sensor is an idea I had to control the display brightness and possible also the wand brightness depending on the ambient light. There is no code yet, it is something I plan to experiment with soon. I added it to the schematic just in case it turned out to be useful. You can never have too many features. :-)
The light sensor could also be an infrared detector which you could use to start the wand by using an infrared light pointed at the wand. How useful??? I don't know, It was cheap to add to the PCB so I thought I would put it on there.
I am also almost finished with my latest PCB design. It now has a 2Amp power supply on the same PCB. This makes the whole thing easier to build, not as many wires to hook up or parts to get. It'll probably be September/October before I have those PCB's though.

ThomasKlee64, 2021-07-27:
I tried to test the function with the frame sensor yesterday, unfortunately without success. I could not find a function with the GPIO pin 32 in the program code. Is this part of the program still missing?

ThomasKlee64, 2021-08-03:
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

Closed 2021-08-03.

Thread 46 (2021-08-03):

No Function of the frame sensor

ThomasKlee64, 2021-08-03:
@Hello Martin,

I tried to test the function of the frame sensor input, unfortunately without success. In the program code the input pin is "22" but in the schematic it is "32". What is correct now. I have changed the 22 to 32 in the program, but there is no reaction when the input is connected to GND. Can you help me here?

MartinNohr, 2021-08-08:
I haven't tested that in over a year. It did work at some point in the past. I'll look into and see what happened. Thanks for letting me know.

MartinNohr, 2021-08-08:
The correct value for the GPIO is 32.
Did you set "Frame Counter:" in the menus to something other than 0? The 0 value means to ignore. It is the number of pulses required to advance one frame.

MartinNohr, 2022-04-05:
I believe this works now so I'll close this issue. Just reopen it if it still doesn't work for you.

Closed 2022-04-05.

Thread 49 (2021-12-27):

image preview option glitch

DaveStu, 2021-12-27:
I've just flashed v2.03 and the option to scroll and preview images has started to glitch for me.
In the previous version (v2.02 I believe) worked perfectly.

When I scroll to preview next image, it flashes and reverts back to previous one.

Btw, this feature is really smart. The features and tweaks just keep getting better and better.

MartinNohr, 2021-12-29:
Try 2.09. There were some problems I fixed.

DaveStu, 2021-12-30:
Ok, will try it next. Just waiting for a SDCARD board, as I've damaged the pads on my first one and cannot find any traces to connect to.

DaveStu, 2022-01-06:
Well new SDCARD board arrived, connected it up and all was well with the prevous code.
Tried to then flash your latest code and the TTGO says "ESP is not in flash boot mode" with ESP home flasher.
I've tried different cables checking connections for any shorts, now I'm stuck.
I'm sure its a driver issue, so tried to clear them but to no avail. Frustration doesnt't even describe things.

DaveStu, 2022-01-24:
Version 2.21 is a night and day difference in dial interaction, I find it glitch free and wonderfully responsive.
Kudos to the effort Martin.

MartinNohr, 2022-01-24:
It took me all day but I finally got the dial working right! Time well spent though, it's a delight to use now. Glad it's working for you too.

DaveStu, 2022-01-26:
I see, glad no one asked me to code it then...eternity. It's definately a delight to use. It's great for all.

MartinNohr, 2022-01-26:
Dealing with mechanical switches that bounce is always fun! I should have debounced it in hardware on my PCB, but that also have meant more parts for the hand-built people, so I decided it was 'easy' to fix in software. :-)

MartinNohr, 2022-03-05:
I'll close this one, it seems to be working very well now.

Closed 2022-03-05.

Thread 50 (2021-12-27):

PCB and components

DaveStu, 2021-12-27:
Hi Martin, Hope your chrostmans was good. I was wondering If one could get the gerber pcb files, and also if BOM + CPL lists are available, so I could get the PCB printed by JLCPCB?

My handmade board is too fragile to be used in the field and requires a more professional, robust board

Thank you

tobias966, 2021-12-29:
Hi Dave,

you can order the PCB there

https://www.pcbway.com/project/shareproject/Magic_Image_Wand_V2_with_PowerSupply.html

Regards
Tobias

MartinNohr, 2021-12-29:
That is the bare pcb of course. PCBWAY won’t let you order single populated PCB’s. I think you have to order 10 at a time, which is what I do, well, actually I order 20 sometimes.

I have a new design of the PCB, but I haven’t got the samples back yet so I don’t want to make it public until I have a chance to test it. No major changes to it though. I moved the power supply components to make it easier to put heat sinks on and I added another connector that I need for my remote camera control and my 3D printer filament weigh scale. I use that PCB for multiple projects.

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

MartinNohr, 2021-12-29:
https://usa.banggood.com/LILYGO-TTGO-T-Watcher-BTC-Ticker-ESP32-For-Bitcoin-Price-Program-4M-SPI-Flash-Psram-LCD-Display-Module-p-1345292.html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
Here is another one that would be nice. I have actually ported the code to run on a card with this display and a touchscreen. I didn't really like the touch screen, it always needed two hands, but perhaps a version with the large screen and my rotary dial would be good. I'll work on that some more next year.

MartinNohr, 2021-12-29:
Here are the gerber, BOM, and pick files for the onboard power supply PCB.
https://github.com/MartinNohr/MagicImageWand/tree/main/MIWNPS1_2

MartinNohr, 2021-12-29:
This board is available and would be pretty easy to move the code to.
https://www.aliexpress.com/wholesale?catId=0&initiative_id=SB_20211229110930&SearchText=ttgo+t4
It has a lovely 320x240 display. It does not have touch screen, but I'm not convinced that is really useful. It would be easy to connect a power supply and the rotary dial and the LED outputs to here. A PCB could designed that this card can be plugged onto. Notice that is has the micro SD reader already there.

DaveStu, 2021-12-30:
OK, I'll perhaps wait for your updated PCB design, though perhaps pointless for me as you use the PCB in other projects too.
As you've said, PCBWAY wont let you order single populated or a few, So I thought I'd try JLCPCB.
Thanks for the BOM list.

That board from Banggood is the same one from Aliexpress, someone has just designed a case for first one.
Seems decent in screen size though.

MartinNohr, 2021-12-30:
The new pcb has a nicer layout for the power supply parts, otherwise it hasn't changed much. I have 3 of those ttgo t4 boards. Lovely displays. I've been planning to port the code to it. Sent from my Verizon, Samsung Galaxy smartphone
-------- Original message --------From: Dave ***@***.***> Date: 12/30/21  7:57 AM  (GMT-07:00) To: MartinNohr/MagicImageWand ***@***.***> Cc: MartinNohr ***@***.***>, Comment ***@***.***> Subject: Re: [MartinNohr/MagicImageWand] PCB and components (Issue #50)
OK, I'll perhaps wait for your updated PCB design, though perhaps pointless for me as you use the PCB in other projects too.
As you've said, PCBWAY wont let you order single populated or a few, So I thought I'd try JLCPCB.
Thanks for the BOM list.
That board from Banggood is the same one from Aliexpress, someone has just designed a case for first one.
Seems decent in screen size though.

—Reply to this email directly, view it on GitHub, or unsubscribe.Triage notifications on the go with GitHub Mobile for iOS or Android.
You are receiving this because you commented.Message ID: ***@***.***>

MartinNohr, 2021-12-30:
I think that JLCPCB also has some minimum limit of assembled boards.

I always have some here, but shipping costs from US to the rest of the world are very high. I sell a PCB for $35 and it often costs $45 to ship it with the post office. I don’t know any way to make it cheaper.

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

DaveStu, 2022-01-01:
Hi Martin, what format or tool did you use to export the BOM and P&P list, as I can only view the CSV and trying to save leaves a file with data thats jumbled and not tabulated?

Indeed, JLCPCB have a minimum of 5 boards. PCBS alone woud cost around $10 shipped to UK, but components more.
Me buying depends on their price

MartinNohr, 2022-01-01:
I just exported those files from EasyEDA. They are a standard CSV (text with columne) type format. I can read them with either Excel or NotePad++. Just make sure if you make any changes in Excel to save in CSV or it will be converted to Excel and then it will not be in CSV anymore and in fact might appear jumbled! I can sell you the populated/tested PCB for $35, but the shipping is a killer. $40.85US. If you know anybody else that wants one I can fit at least 3 in the small flat rate box. Maybe 4, but I've never put more than 3 in there.

MartinNohr, 2022-01-01:
Interesting, I was just looking on the USPS.com site. It appears they have a 1st class package service to UK for $16.25. I haven't used it before, it might be slow, but the price is certainly interesting.

MartinNohr, 2022-01-01:
Re the 1st class package to UK... Actually I have used it, just not to the UK, I sent some PCB's to Canada with that. It took 3 weeks to get to Edmonton, but the price was good. So that is an option that might be worth considering.

MartinNohr, 2022-01-03:
I have been looking at the TTGO T4 some more. I have a couple of them here. It would be easy to port the code to, but looking around the internet I am worried about the availability of this board. It is only sold a couple of places so unless that changes this card my not be available in the long run.
A more interesting idea may be to use the M5. I have already ported the code to it. It would be easy enough to make a little PCB that has the rotary switch (which I still prefer for ease of use) and the level translator drivers for the LED's. The M5 has a lovely display. You remove the bottom plate and then it could plug directly into another PCB with the dial and drivers and perhaps even a nice powerful 5V regulator.

DaveStu, 2022-01-11:
Indeee, that TTGO T4 is very limited in availability, I noticed that too. Are you refering to the M5stack core2 esp32?

MartinNohr, 2022-02-09:
Yes, that is the one, the grey one that has physical buttons. The white one has touch screen buttons and I don't like them as much, too hard to use in my opinion. I have an early version of the code working on it, it's not up to date but it does show how it works with a redesigned menu system.

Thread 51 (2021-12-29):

reboot necessary

tobias966, 2021-12-29:
Dear Martin,

today I used the first time led stripes on the MIW. I have the software version 2.07 on it. When it boots and the version appears on the ttgo also the led on the stripe (I have only on mounted) runs with rainbow color from start to end and back. So for me everything is right. The point is, that I can´t run the images on the led. The preview and all other menues etc. are working, but the led strip doesn´t react. Only after reboot, with the reboot function in the menu it is working.
It doesn´t matter if I put the power with USB C directly on TTGO or with the battery power over the PCB. Batterypower I use 2x 18650cells in line.

With the batterypower I have another phenomen. The TTGO doesn´t start. I can meassure 5V on pin1 and 3,3V on pin12 also I have 5V on D1 top or on PCB points LED3 and LED4. So for me it looks fine. But I have to press, the small reset button on the side. I don´t have added the frame sensor or any other things on the pcb, just one led stripe at LED1, could this be the reason?

Hope you can support.
Tobias

MartinNohr, 2021-12-29:
Not sure. I run 1 LED strip most of the time and it works fine. Have you tried any older versions of the software? I might have broken something with all the changes I made. You can also try “factory reset”. Hold the dial button down while applying power.

If the rainbow pulses when you turn it on then it indicates that the LED strip is working correctly. And if the preview of image files work then the SD card reading must also be working.

Do any of the built-in patterns work? Does the lightbar function work?

The frame sensor isn’t used unless you have enabled it in the menus. That’s why I suggested to do a factory reset operation.

Are you using the WS2812B with 144 LED’s?

Does the progress bar move when you try to show an image? Or what exactly does happen?

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

MartinNohr, 2021-12-29:
One more question: So it works when powered from USB without batteries?

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

MartinNohr, 2021-12-29:
I am wondering, did you set the controllers to 2 and then display an image file of 144 characters? That would give the exact symptoms you are seeing. The rainbow would show on start, and the preview would work. The actual LED display would fail because LED1 is the pixels above 144, which aren’t there if the image is 144. You could enable the image doubling command to make it work.

About the restarting though I have no idea, I have never seen that. You might try a different TTGO.

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

tobias966, 2021-12-29:
Dear Martin,

I checked no several things. The behavour is always similar. It doesn´t matter if power from battery or usb without batteries. I also checked another led strip both with 144led , WS2812B. The controller set is 1. Also factory reset doesn´t help.
During first start I see rainbow over the complete length of the strip. Preview is also working. But when I want to show the image, only the first 6 leds are working. No difference between built in pattern and images from sd card. When I change to light bar all colors exept green are only working with the first 6 leds. When I increase HSV to 10 or more the 7th led is lightning in green. This stops after HUE150 then only the first 6 leds are working. After reboot everything is working.
In the next days I will build up another pcb, will check what happend after. Because this is the only thing, which I don´t changed up to now.

MartinNohr, 2021-12-29:
It is very strange that it shows the rainbow on startup. That means it can write to the LED's. Have you tried any of the built-in patterns?

tobias966, 2021-12-29:
yes built in patterns have similar behavour. Let me try a new pcb in the next days. Honestly I can not explain which influence it should have, but we will see, also I ordered a new ttgo hopefully it will come in the next days.

MartinNohr, 2021-12-30:
The only time I have seen anything like that is when I had long LED wires and my original PCB had the wrong kind of driver chip on it. I looked at the LED data line and saw that it had lots of "ringing" and noise. If you have an oscilloscope you could take a look at the data and power lines on the LED.

tobias966, 2021-12-30:
I have no oscilloscope but after 10th I will check it in my company, hope they will support me. With driver chip you mean the U1? This is from nexperia similar like in your bom. Should I add additional resistors or the 100k resistor on the pcb are enough?

tobias966, 2022-01-05:
I meassured the signal with the oscilloscop. Directly on the pin7 (2LED1) at the ttgo pcb. Also I meassured the signal on the pcb with power supply and on my experience board, where I have only connected the rotary button and nothing else, power supply was with usb direct on ttgo pcb.
Softwareversion was 2.10 and the file which I started was Mario1 which I got from you when I bought the imagepainter from you (last year).
signal after start
https://user-images.githubusercontent.com/73199898/148271391-4cf865b6-5b59-4c09-ae7b-56d9b843cb2f.mp4
signal after reboot
https://user-images.githubusercontent.com/73199898/148271409-08d41c99-07a3-4029-8b26-8b8dd64d998b.mp4

I checked also another ttgo with newest software version 2.16 but with this version reboot doesn´t help. The led are not working, similar behavior as with 2.10 before the reboot.

Is there any possiblity to find the software version 2.10 because I don´t want to change the ttgo with 2.10 to 2.16 to check if it is also not working anymore, but then I have no possibility to lightpaint.

During the start of the ttgo when the rainbow led comes, the signal is also not complitly the same between first start and reboot start.

All measurements I have done without led stripe connected.
Hope this helps you to support me, to find out the root cause.

tobias966, 2022-01-05:
https://user-images.githubusercontent.com/73199898/148274389-4ed81d8f-54f6-4fa3-b9a3-188acb8fcf8d.mp4

First movie is not working, so again, signal after start

tobias966, 2022-01-05:
>

https://user-images.githubusercontent.com/73199898/148274611-941cd9f6-62b5-4d17-9fb6-508e51d32db7.mp4

tobias966, 2022-01-05:
https://user-images.githubusercontent.com/73199898/148274647-f05e47af-0a04-4cbf-8372-2db61a75fb67.mp4

tobias966, 2022-01-05:
https://user-images.githubusercontent.com/73199898/148275254-7bd29bdb-9acb-47b7-baa8-e50905272406.mp4

tobias966, 2022-01-06:
I found software version 1.28 on my hardware. With this software it works without reboot function. So I think there is something different in software code between 1.28 (works without reboot), 2.10 (works with reboot) and 2.16 (doesn´t work, no matter if rebooted or not).
If you want I can make also a small video with output signal of version 1.28

MartinNohr, 2022-02-18:
The 100 ohm resistor is to minimize the ringing on the lines. The signals on the 'scope look ok. I'm puzzled and confused!
The LED strip does need to be connected to really see the signals, put the probes right on the LED connector. Check the strip voltage also, it should be very close to 5V.

MartinNohr, 2022-02-18:
What brightness level are you using? USB power won't run them very bright.

tobias966, 2022-02-20:
the brightness level is 25. Changing to 5 makes no difference.

tobias966, 2022-02-21:
check the strip voltage it is always 5V also no power drop (don´t see on oszi) during the start. Also no difference if you use external usb power or the pcb power
still have feeling to use some wrong libaries. Most influence i found with esp32 board controler. Can you tell which version you use for the board controller?

MartinNohr, 2022-02-21:
Try the binary file that I compiled. It is here on GitHub.
Here are my settings from VS2022.
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
How do I tell which board controller I'm using?

tobias966, 2022-02-22:
thanks I will check. Up to now I´m using arduiono IDÈ. I will try also VS2022 and see how find the info in VS

tobias966, 2022-02-22:
I tried the binary file (sorry didn´t know that this is available). With this it works, so no reboot necessary. Thanks to give this idea.

MartinNohr, 2022-04-24:
Since the binary version works, it must be some kind of library issue.

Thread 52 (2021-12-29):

Dial problem with on-board power supply PCB

MartinNohr, 2021-12-29:
I noticed a problem with the dial incorrectly reading rotations and clicks when running from batteries. Rotating the dial fast will cause it to start reading phantom clicks and other things. I thought it was a software issue, but it never happens when running from USB power. I am investigating noise on the switch lines from the power supply. It might be necessary to add some R or C elements to the board to fix this. I will post the solution here when I have it.

DaveStu, 2021-12-30:
I've concluded something similar and from investigations, it seems the LM2596 buck converter board I'm using from the original MIW parts list could be the culprit. Apparently the ripples could be quite high and datasheet suggest the output capacitor needs changing depending on voltage requirements.
Not sure how it setup on your PCB though.

MartinNohr, 2021-12-30:
My 'scope shows the 5V is clean and so are the dial and switch lines. So I don't know exactly what is going on. It does seem to only happen after previewing the image, but it also only happens when running on battery power. This is proving to be a hard one to find. I have made some interrupt code changes that seem to make a little bit better but it still happens.

DaveStu, 2022-01-01:
I see, It's just what I found in forums. I haven't got a scope to analyse so I'll assume it's not the buck converter.

MartinNohr, 2022-01-01:
Happy New Year to you and all around you.
It is certainly odd that the quickly rotation dial can go weird but only on battery power. It certainly smells like the power supply, but on my 'scope it looks fine. I wish it would show the problem when running on USB power, then it would be trivial to find and fix. Oh well, maybe this year I'll figure it out... :-)

DaveStu, 2022-01-08:
code v2.15 seems much better on battery power than before.

MartinNohr, 2022-01-09:
I have now seen the same problem using USB power, not as often, but it does happen. So I can now see what happened. The click dial input gpio always reads 0, but the port is actually high. Very strange!

DaveStu, 2022-01-19:
I wonder if its different for you, because I'm not using your PCB but more simpler connections and less components?
Although it's not glitche free, as you've experienced.
I read a long while ago about pullup resistors and rotary encoders, that the esp32 dont neccesarily need external ones, as you can activate internal ones? I made a note about the code being enc_internal_pullup and setting this to -1 would activate them. I'm not a coder, Is that something you've done or we need?

MartinNohr, 2022-01-19:
I am using the internal pullups, although they are not available on ports 34-39 (if I remember correctly). It is handled in code, if you look in rotarydialbutton.h in the begin() function you will see where the direction and the pullups are enabled.

I have fixed it now, I monitored the switch with my ‘scope and found that while showing the preview and rotation the dial fast the push button input turns into an output. I am thinking this might be some quirk in the esp32 TTGO hardware. Anyway, I worked around it with a little software and by moving the push button contact to a different GPIO pin. I used 35 which is input only!

BTW, I have seen the problem even when running with USB power, so I don’t think the onboard power supply is really the issue. Although, it is harder to do with USB power. I looked at all the voltages with my ‘scope and everything looks fine. I am suspicious of the SD code which is heavily used when previewing the image. I am using a very old version of the SD code. The newer versions are not compatible with the old one so I haven’t upgraded. I suppose I should do that. It might fix the problem.

Martin

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

DaveStu, 2022-01-19:
I had a look, pardon my ignorance, you are right about the pullup code. It's not something I ever work on, just read about.
I am certainly learning though.

Thats interesting about the SD code, again, you are the master at this.

MartinNohr, 2022-01-23:
It appears to actually have been a problem in my interrupt handling code, I'm not sure exactly what, but version 2.21 seems to be working perfectly on battery or USB power. I rewrote the dial interrupt handling.

Closed 2022-01-23.

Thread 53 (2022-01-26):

preview of 288 pixel bitmaps

MartinNohr, 2022-01-26:
Preview of 288 pixel bitmaps is broken. Scrolling causes very strange effects.

DaveStu, 2022-01-26:
Indeed it does. Mine seems to duplicate about 20-25% of the image on the right hand side.
Not a deal breaker and certainly usable.

MartinNohr, 2022-01-26:
It's a "little" math error! I'll fix it soon. ;-)

DaveStu, 2022-01-27:
No rush, the main culprit was the dial interaction, that issue did get annoying

MartinNohr, 2022-01-27:
I've almost got it working, just a little arithmetic problem when scaling down to 144 from 288. I should have it fixed in the next couple of days.

MartinNohr, 2022-01-27:
Fixed. It works for me now! Let me know if any problems are found. I'll leave this issue open for a few days.

MartinNohr, 2022-01-31:
Since it seems to be ok now, I'll close this thread.

Closed 2022-01-31.

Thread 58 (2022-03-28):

many built-in functions don't allow the frame hold time to be changed after the first use

MartinNohr, 2022-03-28:
The first time a built-in function is run the current frame time will be used. If the frame time is then changed and the function is run again it will still use the original frame time. It is necessary to reboot and change the frame time first before running the built-in function. The problem has been identified and is due to a static instantiated class in the fastLed library. A fix will be coming soon.

MartinNohr, 2022-03-28:
Fixed in 2.29 version.

Closed 2022-03-28.

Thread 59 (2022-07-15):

TTGO T4 Version

MartinNohr, 2022-07-15:
There is a nice esp32 board available with a 2.2" 240x320 display called the TTGO T4. I have been working on porting the code to this board and it is almost working. It even has an IMU chip that can be used to show whether the wand is level or not. The display is beautiful. I will post more information here as I finish the development of the code.

MartinNohr, 2022-07-17:
It is now working reasonably well, lots of testing is needed of course, and some button presses might need to be redefined to be more useful.

DaveStu, 2022-07-20:
Hi Martin, hope you're doing well, its been a while. Seems like you're full steam ahead with the T4 port of the code, excellent.
I've been enjoying the use of my esp32 based version as image painter of course but also impromptu light bar using it to light various colours as accents lights in photography.

I have a couple of old android phones, which are not worth much in resale, so use them as wifi only devices for testing apps or even as a light usage NAS, or smart controller for lights and switches etc.
From that I had a crazy idea recently, although we dont need to implement it.

Imagine using a spare android phone as your interface to the esp boards, that giant screen in comparison
The code would obviously reside on the esp, but perhaps the phone is the commander and dictates code too.
Ideally hardwired so connectected via its USB port to the esp.
I've been playing around with WLED and their app, hence the crazy idea I had.
Anyway, its not really required, I'm just a crazy thinker

MartinNohr, 2022-07-27:
It is working on a T4, feel free to try if you have one. It does need a little refinement on the button use. It uses the 3 buttons on the T4 instead of the rotary dial. I could hook up the dial but there aren't very many pins available on the T4 connector. It's very nice having that large screen.
I actually did have a ble phone app working with the MIW. We commented the code out because the guy in germany added the rudimentary web interface. BLE and WiFi can't be used at the same time.
However, I could get busy and refine the web interface to handle everything, it only does a few things right now. Using a web interface means a computer or a phone could be used to control the MIW. I'll start thinking about that again. Right now it does allow up and download of bmp files. It can adjust a few of the settings, I need to add some code to handle all the settings, then I think it might be useful. The display is certainly better. I think I already have it displaying the list of bmp files, but I haven't used it in a while.
I suppose you could hardwire it though the USB port, they can be used for serial data but I am thinking that the web interface might still be better.
Good to hear from you again, very few comments these days!
Oh, and your idea isn't entirely crazy!

tobias966, 2022-08-17:
Hi Martin, yesterday my T4 arrived and first look is it works perfectly after I understood working with the 3 buttons. At the weekend I will also use it with the led bars and give you a feedback. Because for me the rotary dial is easier to use at the moment, can I solder this also on the T4. Honestly I don´t check if the I/O´s are available.

MartinNohr, 2022-08-18:
I'll have to define some pins for the rotary switch and enable that in the code. There aren't very many pins available on the T4. I do agree, the rotary dial is much easier to use. I'll let you know when I figure out which pins we can use. Some of them are reserved, even though they are on the connector. Poor design.

DaveStu, 2022-09-02:
I haven't jumped on the T4 train, I'm not sure I need it unless there is a big leap in additional functionality plus a cost issue for board and 3D printing
For me, the T1 screen size is ok, for now. I'll still be checking on progress and any input I can add.

I'm also currently trying to design/invent another gadget, well two. I'd love to be able to get out of this rat race and be healthy and financially stable by making it big and help a few struggling people along the way.

MartinNohr, 2022-09-06:
The only real advantage I can see for the T4 is the larger screen. Now there is a new TTGO T-DisplayS3 that is about the same size but with a slightly larger screen. I've ordered a couple of them to experiment with. Unfortunately it might not work in the existing PCB because while it has the same number of pins, some of them have changed positions. I might be able to work around it with software since the power and ground pins are the same. I'll post a comment when I know for sure.

manussn, 2022-11-03:
Can you help me? I was trying to configure the TTGO T4 wifi through the Arduino IDE and the screen turned off and did not turn on again. I don't know if I reset the EPROM. I'm desperate.

manussn, 2022-11-03:
@MartinNohr  this message was in the prompt.

**Leaving...
Hard resetting via RTS pin...**

MartinNohr, 2022-11-04:
Was this just an update or was it the first time the MIW software was loaded?
The "hard resetting via RTS" is the normal message for rebooting the ESP32.
Did you set the T4 correctly in both .h files? I think I put instructions in the docx file. If this isn't done then the display will not work at all. I suspect that you didn't change the two .h files, one in the MIW code and the other in the display driver library.

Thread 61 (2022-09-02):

Text colour not saving, cannot exit menu v2.42

DaveStu, 2022-09-02:
In latest update (v2.42) not a critical issue although I do use it to make reading in the dark easier.
When I go to options to change colour of text, I cannot save and exit as usual. I've tried buttons, doesn't work so I need to reboot.
This is on TTGO T1.

MartinNohr, 2022-09-02:
Thanks for catching that one, I hadn't noticed it yet. I just fixed it (2.43), please try the latest and make sure it works for you also.
Did you notice I added a feature that will install the bin file from the SD card?

tobias966, 2022-09-02:
I tested it on my ttgo1 V2.43 is working well. Also the new feature with the bin file is great. Saves a  lot of time, because I don´t have to compile every time.

MartinNohr, 2022-09-04:
Glad you like the load from bin file. I even use it myself to install the latest on the several models that I have of the wand. I think it will be very useful to people that can’t or don’t want to compile.

Martin

DaveStu, 2022-10-06:
Hello, yes all fixed now. Since me last input from version 2.42 you've certainly been busy, version 2.75!
First time I used the webserver, very funky and intuitive to use, excellent work. You've certainly put in a lot of work and features already. Although it's not something I need yet, it's a fabulous addition. Though my friend did comment, allowing to upload images straight from the phone is fantastic!
Oh yes, I did see the bin file upload feature, thats very useful indeed. You sir are full of surprises.
Just curious, I wonder what happened to Dirk?

MartinNohr, 2022-10-06:
I like to keep busy! Glad you like it. I’m pretty happy with my design, although I still have long list of things I want to improve. Doing this kind of thing keeps my mind sharp, I believe so anyway. I’m a retire software engineer (I’m 72 now), and I used to design analog and digital hardware. After my MSc EE, I went to Bell Northern Research for a few years (middle 1970’s). They were the Bell labs of Canada and I learned a lot there.

About Dirk, I have no idea, he’s a smart guy and I have appreciated his input greatly in the past. Dirk suggested the web server interface originally, I was writing a phone app to do the remote control. When he noticed that BLE and the web server wouldn’t happily work together I abandoned the phone app work. The web server is more general since it works from any browser, not just a phone. He hasn’t posted anything in a long time. I never had his direct email address, if I did I would try and reach him. He does seem to have just disappeared. I’ll let you know if I ever hear from him.

So what are using the MIW for?

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

DaveStu, 2022-11-11:
"So what are using the MIW for? "
So far, I've testing/using it with some of the wedding couples, so create something different, thouugh that is a very occasion due to not having many booking.
Then also, I've been struggling with mental health for many years and I try to create or involve in such project, some for simply pure enjoyment and others to be able to learn new things and also enjoy photography, a hobby I use for my ,mind state, this MIW has allowed me to experiment in a different way and different time of day.
Recently I have had interest with a fellow photography, who wants to calibrate on some projects, with me helping her to create some unique light painting patterns, so this is where it's going too..

I've been trying to rework the handle design on mine, currently being round I find it a weak point, to try and create a sturdier grip, like a grab handle to easy to hold with one hand, and perhaps move or duplicate the "execute"button to handle in a ergonomical way that can easily be pressed.
Also how I could design something, that quickly allows me to attach a wheel or two to the bottom of MIW, like chunky 4" pneumatic wheels, which also are height adjustable (perhaps like a tripod height adjusting clamp mechamism).
Perhaps even a 4 wheel system, like a skateboard but with smother softer air filled wheels.
I can then roll the MIW along the contours of the ground, especially if its curved, to create more accurate images, especially when trying to create short animations with bmp frames, when I need to repeat the same moveent many times. I came to the idea from videographers who use sliders or dollys.
I originally did think of gyros but thats far too complicated.

MartinNohr, 2022-11-15:
I'm glad you are using the MIW in several ways that are helping you and making you more creative.
Have you looked at my handle design? I find it easy to hold and the button is right under my thumb so it is easy to use.
I do like the wheel idea, I've been planning to design something like that with an encoder to advance the frames. I'm also designing a new PCB that has a motion detector/orientation sensor onboard. This will also allow the frames to be advanced according to the wand motion. It will take a bit of calculus, but it isn't too complicated to do the math. The faster you move the fast the frames will change! But of course using a wheel also lets the wand follow the ground and might be better. There is already code that advances the frame with each pulse from an encoder wheel. I just need to design a wheel using an encoder.

DaveStu, 2022-11-17:
I have indeed seen your handle design, it's now sort of where I've landed, after experimenting. I would have used your files, but printing was/is too expensive especialyl for strong plastics. So, as I like making thinks anyway, as I've always enjoyed DIY, woodwork and mroe, I put something rudimentary together
Ah I see, you've been working on a wheel idea too, excellent. I like the advancing frame idea, is that for automation?
As in, would the camera take the next image too automatically. Whats your thinking behind it on how to use it, I'm intrigued?

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

MartinNohr, 2022-11-17:
I printed with PLA, it was plenty strong. Cost a couple of dollars in filament. But of course you have to have a 3D printer.
By "frame" I meant a column of the BMP image. As the wheel rotates the encoder pulses the input to the MIW. Each pulse makes the MIW move to the next column in the BMP image. It provides perfect column advancing that uses position instead of the "frame time" in the MIW. The code is already in there for it and I have tested it. It's an option in the image timing setting somewhere, I don't remember exactly what I called it.
I am working on a remote control for the camera. What I've done is used the wireless to fire the camera shutter when the button is pressed on the MIW to play the BMP file. That way you don't have to have someone running the camera. You can do it all by yourself!

Closed 2022-09-06.

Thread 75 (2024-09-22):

Webserver compilation error

NashMerwolf, 2024-09-22:
Hi,
trying to update my project to your TTGO version .
there was alot of problems while compiling with lines :
#86 	//ledcSetup(ledChannel, freq, resolution);
#89 	//ledcAttachPin(tftEnable, ledChannel); that i commented to check back problems.

i hit on this problem concerning ESP32 library :

In file included from C:\Users\xxxxxx\Downloads\MagicImageWand-main\MagicImageWand\MagicImageWand.h:37,
                 from C:\Users\xxxxxx\Downloads\MagicImageWand-main\MagicImageWand\MagicImageWand.ino:8:
C:\Users\xxxxxx\AppData\Local\Arduino15\packages\esp32\hardware\esp32\3.0.4\libraries\WebServer\src/WebServer.h:211:32: error: 'FS' was not declared in this scope; did you mean 'fs::FS'?
  211 |   typedef std::function<String(FS &fs, const String &fName)> ETagFunction;
      |                                ^~
      |                                fs::FS
In file included from c:\Users\xxxxxx\Documents\Arduino\libraries\TFT_eSPI/Processors/TFT_eSPI_ESP32.h:67,
                 from c:\Users\xxxxxx\Documents\Arduino\libraries\TFT_eSPI/TFT_eSPI.h:48,
                 from C:\Users\xxxxxx\Downloads\MagicImageWand-main\MagicImageWand\MagicImageWand.ino:7:
C:\Users\xxxxxx\AppData\Local\Arduino15\packages\esp32\hardware\esp32\3.0.4\libraries\FS\src/FS.h:87:7: note: 'fs::FS' declared here
   87 | class FS {
      |       ^~
C:\Users\xxxxxx\AppData\Local\Arduino15\packages\esp32\hardware\esp32\3.0.4\libraries\WebServer\src/WebServer.h:211:32: error: 'FS' was not declared in this scope; did you mean 'fs::FS'?
  211 |   typedef std::function<String(FS &fs, const String &fName)> ETagFunction;
      |                                ^~
      |                                fs::FS
C:\Users\xxxxxx\AppData\Local\Arduino15\packages\esp32\hardware\esp32\3.0.4\libraries\FS\src/FS.h:87:7: note: 'fs::FS' declared here
   87 | class FS {
      |       ^~
C:\Users\xxxxxx\AppData\Local\Arduino15\packages\esp32\hardware\esp32\3.0.4\libraries\WebServer\src/WebServer.h:211:60: error: template argument 1 is invalid
  211 |   typedef std::function<String(FS &fs, const String &fName)> ETagFunction;
      |                                                            ^
C:\Users\xxxxxx\AppData\Local\Arduino15\packages\esp32\hardware\esp32\3.0.4\libraries\WebServer\src/WebServer.h:211:16: error: '<expression error>' in namespace 'std' does not name a type
  211 |   typedef std::function<String(FS &fs, const String &fName)> ETagFunction;
      |                ^~~~~~~~~~~~~~~~~~~~~~~~~~~~~~~~~~~~~~~~~~~~~
C:\Users\xxxxxx\AppData\Local\Arduino15\packages\esp32\hardware\esp32\3.0.4\libraries\WebServer\src/WebServer.h:212:32: error: 'ETagFunction' has not been declared
  212 |   void enableETag(bool enable, ETagFunction fn = nullptr);
      |                                ^~~~~~~~~~~~
C:\Users\xxxxxx\AppData\Local\Arduino15\packages\esp32\hardware\esp32\3.0.4\libraries\WebServer\src/WebServer.h:229:3: error: 'ETagFunction' does not name a type; did you mean 'OP_Function'?
  229 |   ETagFunction _eTagFunction = nullptr;
      |   ^~~~~~~~~~~~
      |   OP_Function
C:\Users\xxxxxx\AppData\Local\Arduino15\packages\esp32\hardware\esp32\3.0.4\libraries\WebServer\src/WebServer.h:212:50: error: could not convert 'nullptr' from 'std::nullptr_t' to 'int'
  212 |   void enableETag(bool enable, ETagFunction fn = nullptr);
      |                                                  ^~~~~~~
      |                                                  |
      |                                                  std::nullptr_t

exit status 1

Compilation error: exit status 1

any idea ?
best regards

NashMerwolf, 2024-09-22:
Figured out that it was ESP32 core 3.0.4 wasnt supported.
i tried with 2.0.14v and compiled well with lines #89 - 88 - 86 commented//

Work too with 2.0.17 but not 3.0.0

MartinNohr, 2024-12-09:
Yes, I've been using 2.0.17. I have tried to switch to the 3.x library, but the TFT library doesn't work. I'll figure it out eventually! It could be that the TFT library needs some changes too. I'll post an answer here if and when I get it working, meanwhile just use the older esp library.
Really really sorry about the late response, I've haven't been keeping up with my email.

codenamekraken, 2024-12-25:
same problem how to fix it

codenamekraken, 2024-12-26:
> Figured out that it was ESP32 core 3.0.4 wasnt supported. i tried with 2.0.14v and compiled well with lines #89 - 88 - 86 commented//
>
> Work too with 2.0.17 but not 3.0.0

Can you please help me buddy

MartinNohr, 2024-12-28:
I can get it to compile but the display no longer works with 3.x.x. Others have also reported this with the TFT_eSPI library. I have not seen a good fix yet. It might be that the original author Bodmer is no longer maintaining that library. I will check in a couple of  months to see if the library gets fixed. If not I have three options.
1. Fix it myself, maybe.
2. Switch to a different display library, might not be easy, I use the sprites from that library.
3. Stay with board version 2.17. Easy for now, but might be a problem in the long run.
I'll post information here when anything changes.

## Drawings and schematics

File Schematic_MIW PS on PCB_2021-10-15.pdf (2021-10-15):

## Frame Switch is used for an open collector to ground for frame advance

LDR is for a light dependent resistor to control the display LCD brightness.

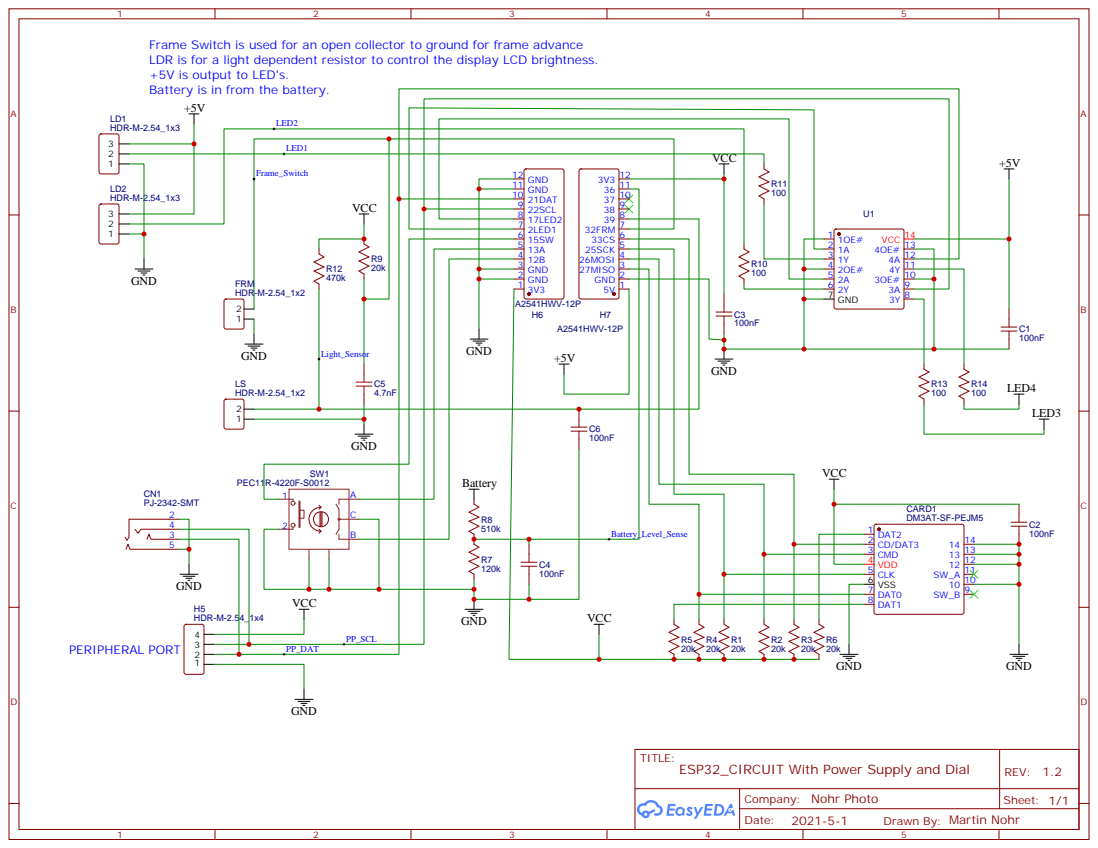
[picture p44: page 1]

+5V is output to LED's.
Battery is in from the battery.

Drawn By: Martin Nohr

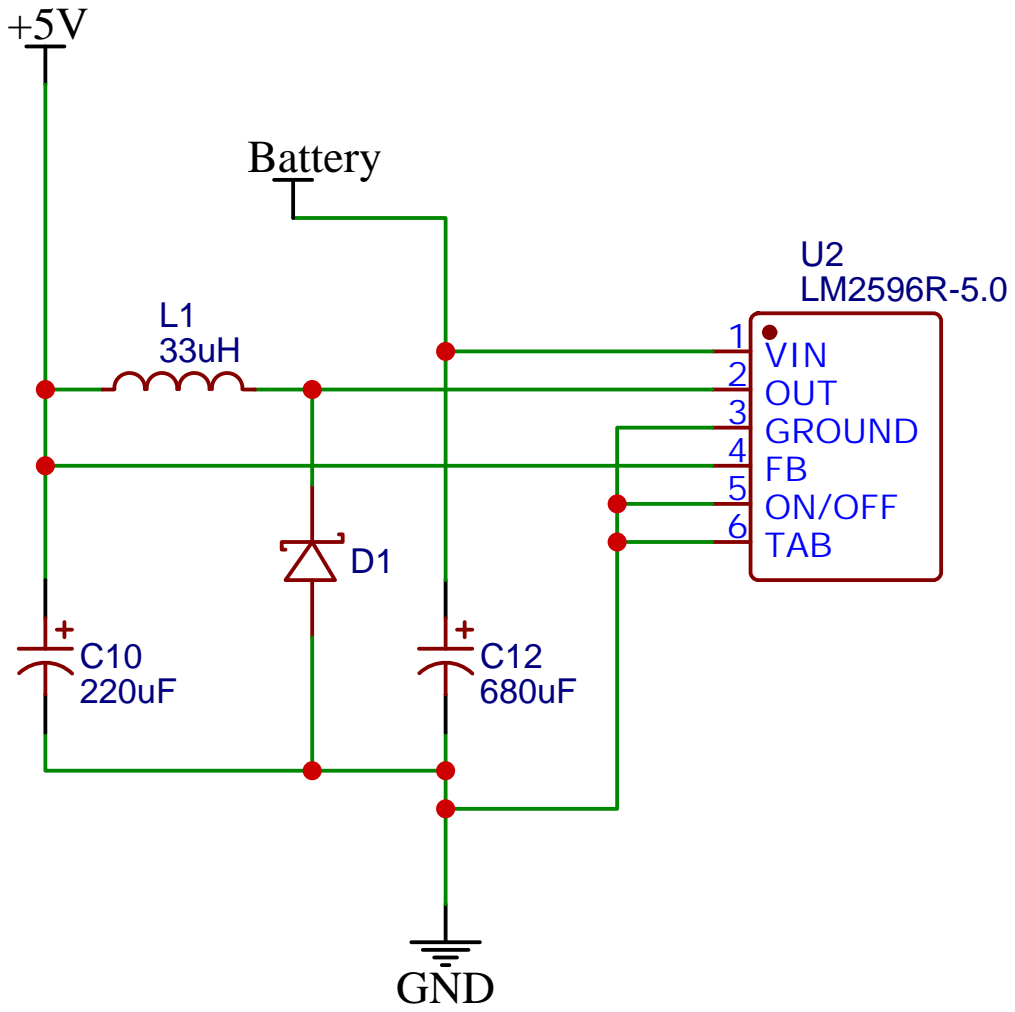
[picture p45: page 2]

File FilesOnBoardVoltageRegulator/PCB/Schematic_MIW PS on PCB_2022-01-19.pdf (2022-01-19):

## Frame Switch is used for an open collector to ground for frame advance

LDR is for a light dependent resistor to control the display LCD brightness.

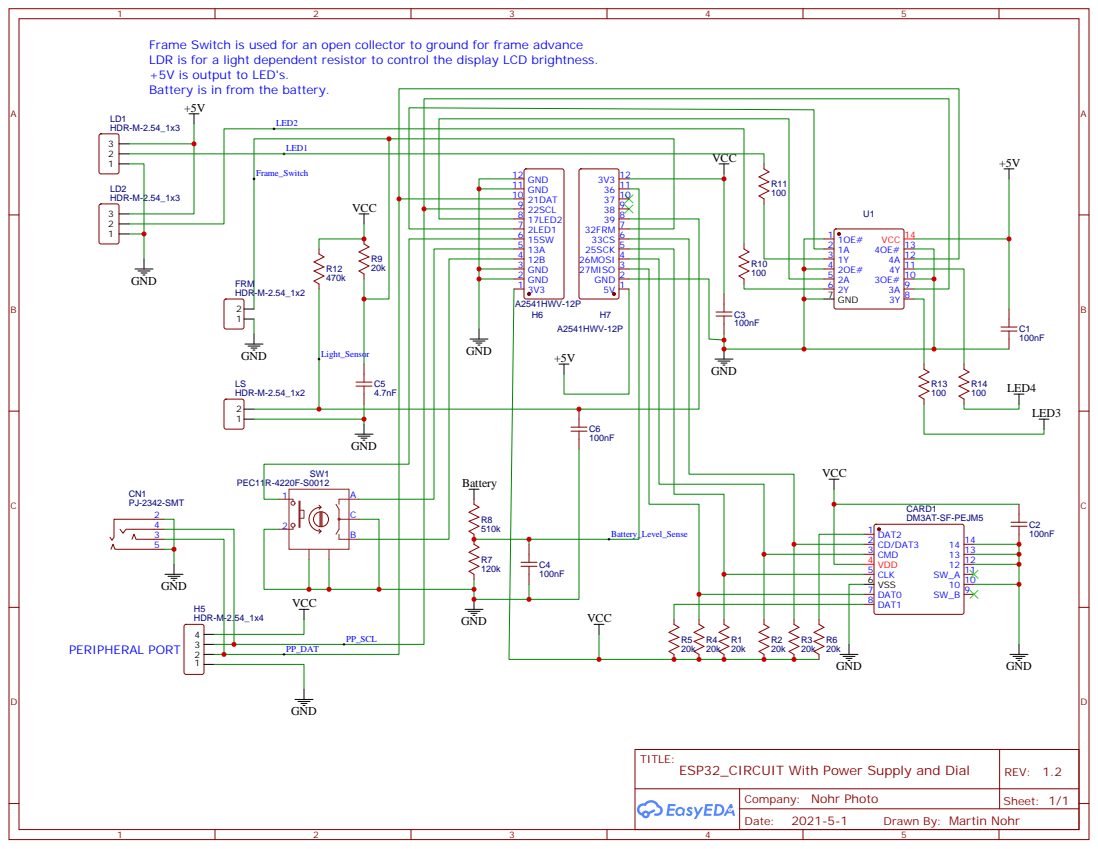
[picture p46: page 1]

+5V is output to LED's.
Battery is in from the battery.

Drawn By: Martin Nohr

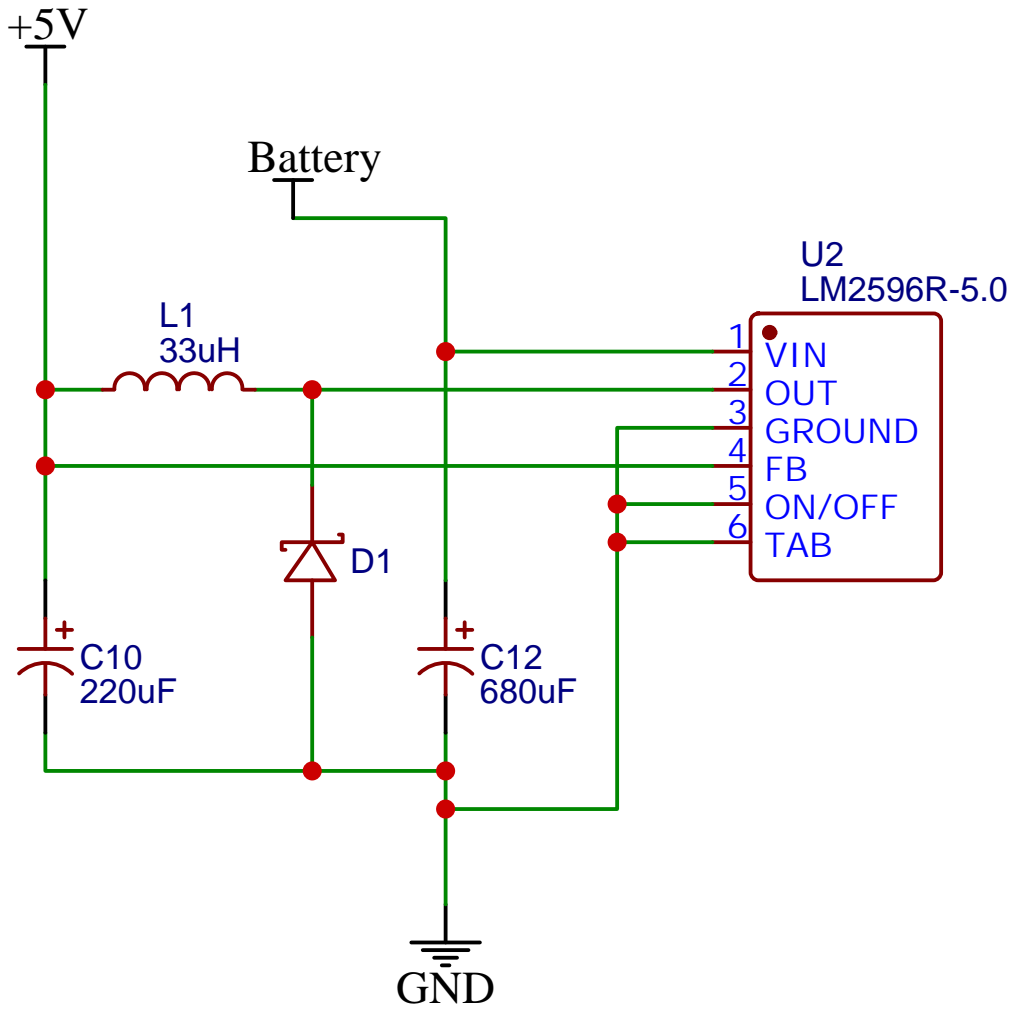
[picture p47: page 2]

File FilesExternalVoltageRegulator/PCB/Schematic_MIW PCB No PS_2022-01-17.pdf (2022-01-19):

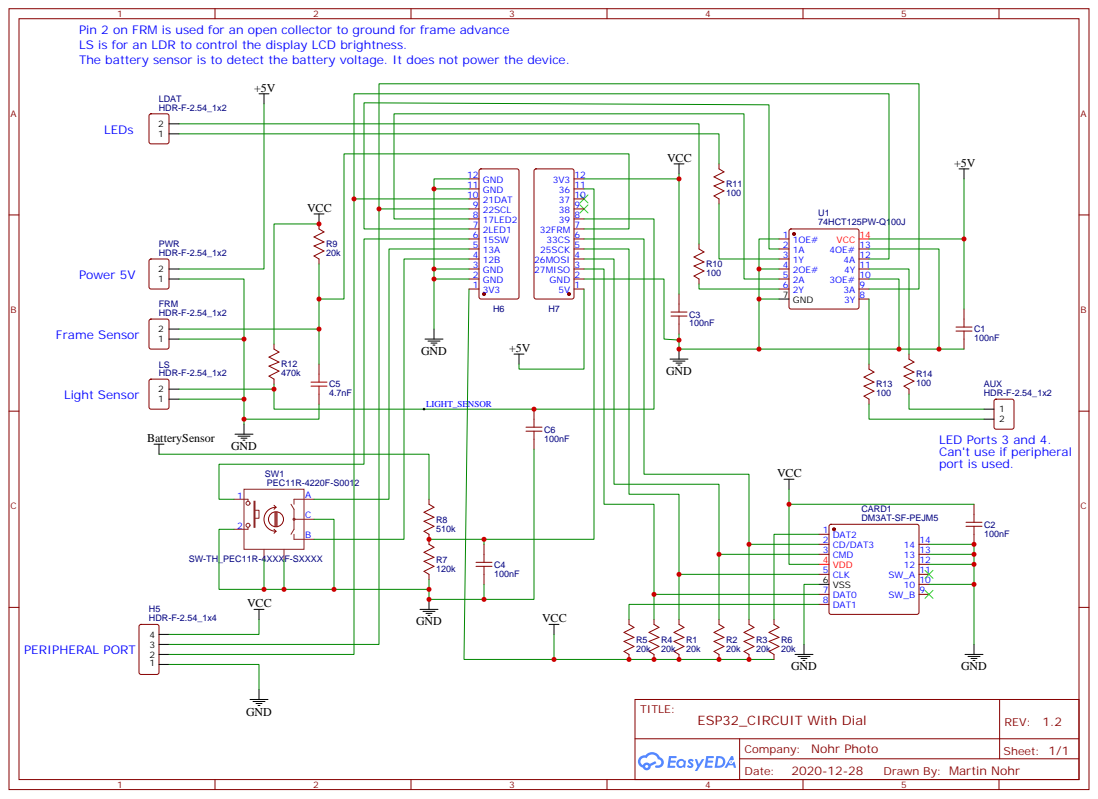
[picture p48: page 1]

Pin 2 on FRM is used for an open collector to ground for frame advance
LS is for an LDR to control the display LCD brightness.
The battery sensor is to detect the battery voltage. It does not power the device.

LED Ports 3 and 4.
Can't use if peripheral
port is used.

Drawn By: Martin Nohr

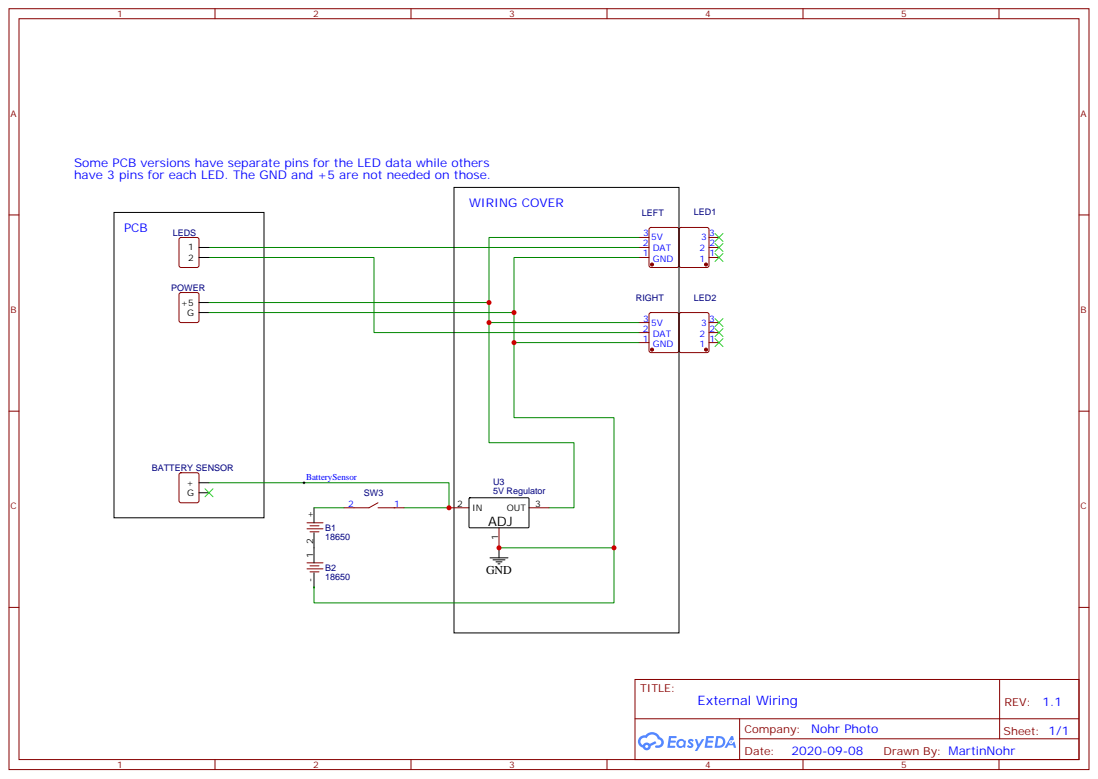
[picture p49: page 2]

Some PCB versions have separate pins for the LED data while others
have 3 pins for each LED. The GND and +5 are not needed on those.

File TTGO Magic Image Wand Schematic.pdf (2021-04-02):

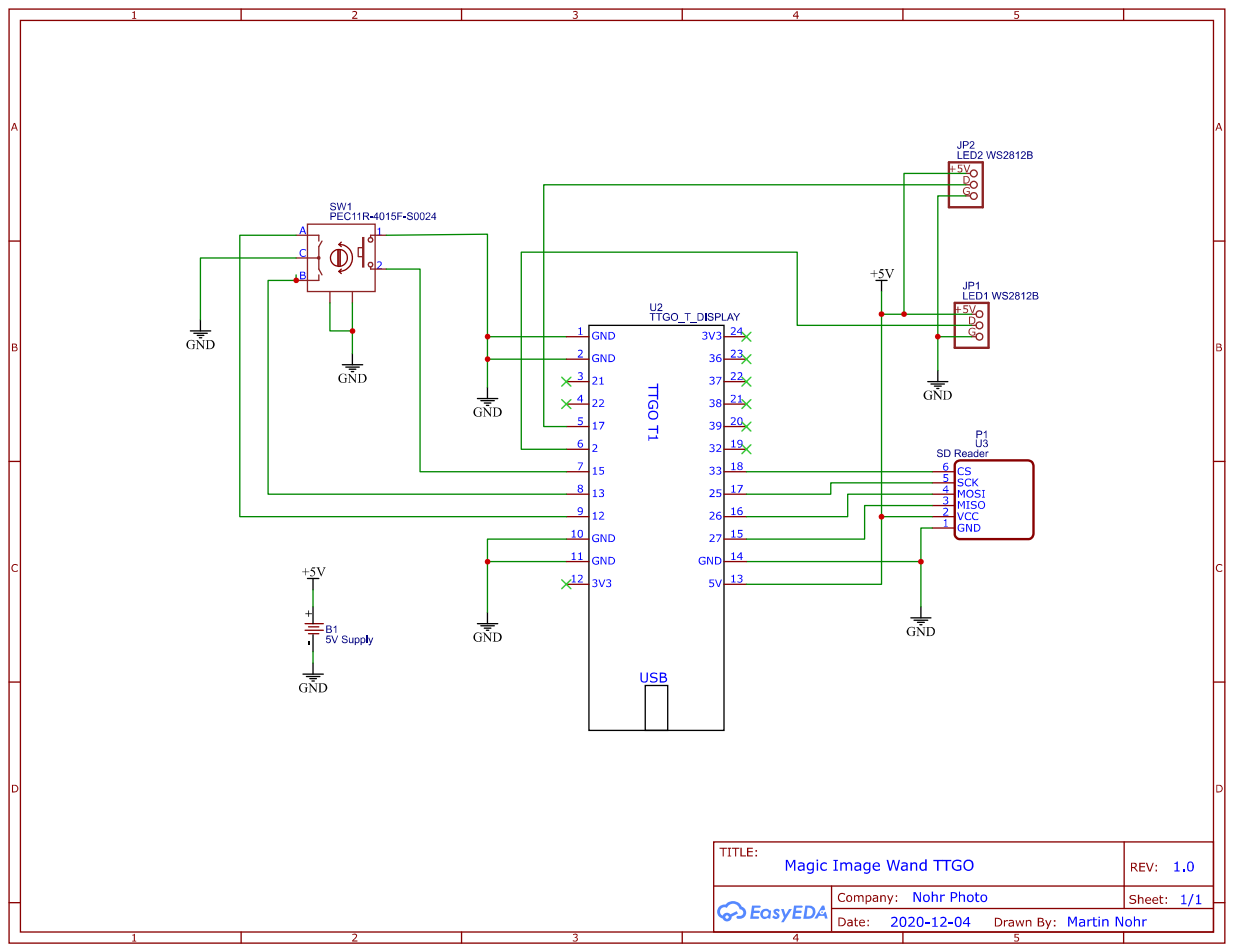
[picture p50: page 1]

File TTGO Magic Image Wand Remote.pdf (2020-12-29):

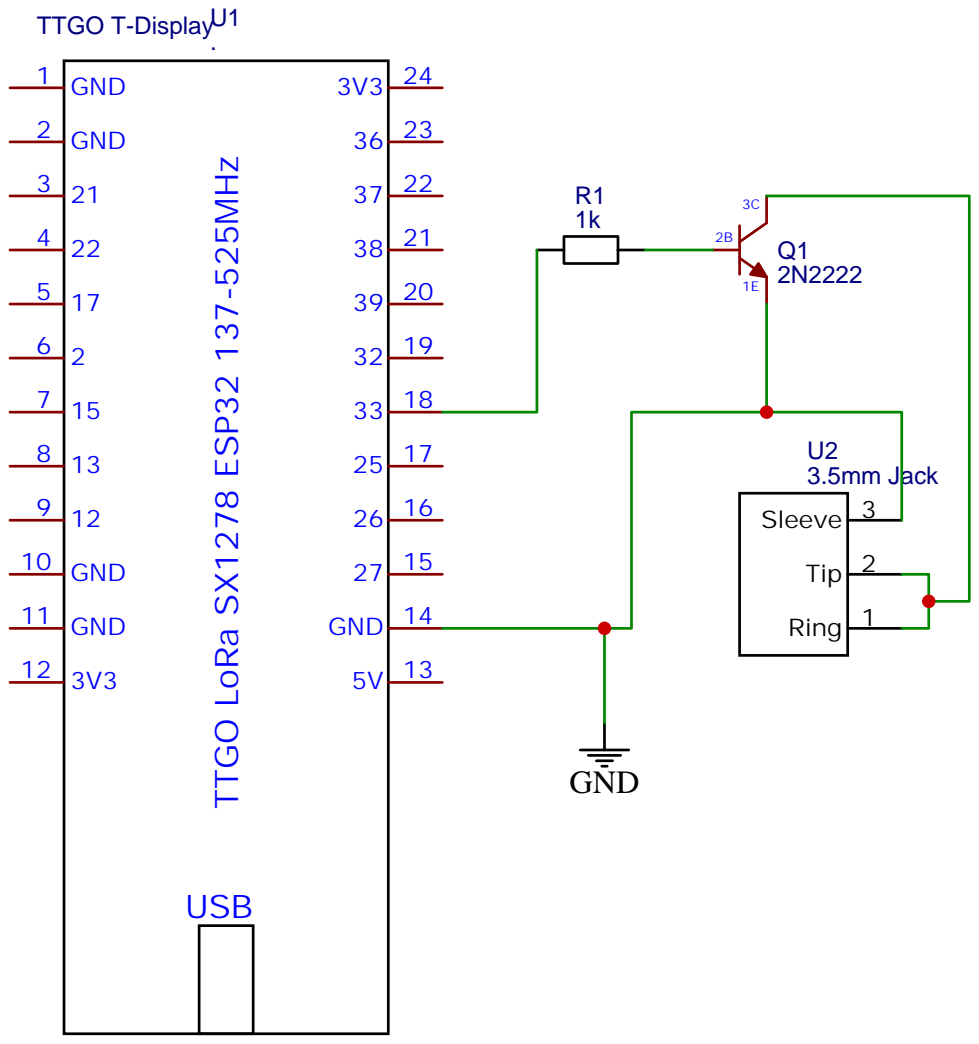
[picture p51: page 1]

Drawn By: Dirk Essl

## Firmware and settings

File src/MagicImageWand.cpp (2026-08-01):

/*
 Name:		MagicImageWand.ino
 Created:	12/18/2020 6:12:01 PM
 Author:	Martin Nohr
*/
#include <Arduino.h>
#include "MagicImageWand.h"
#include "fonts.h"
#include <nvs_flash.h>

RTC_DATA_ATTR static bool bWakeFromSleep;

// some forward references that Arduino IDE needs
int readByte(bool clear);
void ReadAndDisplayFile(bool doingFirstHalf);
uint16_t readInt();
uint32_t readLong();
void FileSeekBuf(uint32_t place);
int FileCountOnly(int start = 0);

//static const char* TAG = "lightwand";
//esp_timer_cb_t oneshot_timer_callback(void* arg)
void oneshot_LED_timer_callback(void* arg)
{
	g_bStripWaiting = false;
	//int64_t time_since_boot = esp_timer_get_time();
	//Serial.println("in isr");
	//ESP_LOGI(TAG, "One-shot timer called, time since boot: %lld us", time_since_boot);
}

// timer called every second
void periodic_Second_timer_callback(void* arg)
{
	if (sleepTimer)
		--sleepTimer;
	if (SystemInfo.eDisplayDimMode == DISPLAY_DIM_MODE_TIME && displayDimTimer) {
		--displayDimTimer;
		if (displayDimTimer == 0) {
			displayDimNow = true;
		}
	}
	// check if about to time out
	if (g_nB0Pressed == 1 || g_nB1Pressed == 1)
		g_bB0B1Cleared = true;

	if (g_nB0Pressed)
		--g_nB0Pressed;
	if (g_nB1Pressed)
		--g_nB1Pressed;
}

constexpr int tftEnable = TFT_PWM_PIN;
// use these to control the LCD brightness
const int freq = 2000;
const int ledChannel = 0;
#if TTGO_T == 3
	const int resolution = 10;
#else
	const int resolution = 8;
#endif
TFT_eSprite LineSprite = TFT_eSprite(&tft);  // Create Sprite object "LineSprite" with pointer to "tft" object
#define BATTERY_BAR_HEIGHT 4
TFT_eSprite BatterySprite = TFT_eSprite(&tft);  // Create Sprite object "BatterySprite" with pointer to "tft" object
TFT_eSprite FileCountSprite = TFT_eSprite(&tft);	// shows the file position and count

void setup()
{
	// init the display
	tft.init();
	tft.fillScreen(TFT_BLACK);
	Serial.begin(115200);
	while (!Serial.availableForWrite()) {
		delay(10);
	}
	//Serial.println(String("wake:") + bWakeFromSleep);
	//Serial.println("flash:" + String(ESP.getFlashChipSize()));
	//Serial.print("setup() is running on core ");
	//Serial.println(xPortGetCoreID());
	// create a mutex
	macroMutex = xSemaphoreCreateMutex();

	// configure LCD PWM functionality
	pinMode(tftEnable, OUTPUT);
	digitalWrite(tftEnable, HIGH);
	// ledcSetup(ledChannel, freq, resolution);
	// attach the channel to the GPIO to be controlled
	ledcAttach(tftEnable, freq, resolution);
	// ledcAttachPin(tftEnable, ledChannel);
	// on the S3 we need to turn on GPIO15 in order to have backlight with batteries
#if TTGO_T == 3
	pinMode(15, OUTPUT);
	digitalWrite(15, HIGH);
#endif
#if TTGO_T == 1 || TTGO_T == 3
	CRotaryDialButton::begin((gpio_num_t)DIAL_A, (gpio_num_t)DIAL_B, (gpio_num_t)DIAL_BTN, (gpio_num_t)0, ONBBTN1, (gpio_num_t)-1, (gpio_num_t)-1, &SystemInfo.DialSettings);
#elif TTGO_T == 4
	CRotaryDialButton::begin((gpio_num_t)DIAL_A, (gpio_num_t)DIAL_B, (gpio_num_t)DIAL_BTN, (gpio_num_t)0, (gpio_num_t)-1, (gpio_num_t)38, (gpio_num_t)39, &SystemInfo.DialSettings);
#endif
	setupSDcard();
	//gpio_set_direction((gpio_num_t)LED, GPIO_MODE_OUTPUT);
	//digitalWrite(LED, HIGH);
	gpio_set_direction((gpio_num_t)FRAMEBUTTON_GPIO, GPIO_MODE_INPUT);
	gpio_set_pull_mode((gpio_num_t)FRAMEBUTTON_GPIO, GPIO_PULLUP_ONLY);
	// init the onboard buttons
	gpio_set_direction(ONBBTN0, GPIO_MODE_INPUT);
	gpio_set_pull_mode(ONBBTN0, GPIO_PULLUP_ONLY);
	gpio_set_direction(ONBBTN1, GPIO_MODE_INPUT);
#if TTGO_T == 3
	gpio_set_pull_mode(ONBBTN1, GPIO_PULLUP_ONLY);
#endif
	oneshot_LED_timer_args = {
				oneshot_LED_timer_callback,
				/* argument specified here will be passed to timer callback function */
				(void*)0,
				ESP_TIMER_TASK,
				"one-shotLED"
	};
	esp_timer_create(&oneshot_LED_timer_args, &oneshot_LED_timer);

	periodic_Second_timer_args = {
				periodic_Second_timer_callback,
				/* argument specified here will be passed to timer callback function */
				(void*)0,
				ESP_TIMER_TASK,
				"second timer"
	};
	esp_timer_create(&periodic_Second_timer_args, &periodic_Second_timer);
	esp_timer_start_periodic(periodic_Second_timer, (int64_t)1000 * 1000);

	SystemInfo.bCriticalBatteryLevel = false;
	tft.setFreeFont(&Dialog_bold_16);
#if TTGO_T == 1 || TTGO_T == 3
	SystemInfo.nDisplayRotation = 3;
#elif TTGO_T == 4
	SystemInfo.nDisplayRotation = 0;
#endif
	tft.setTextSize(1);
	tft.setTextPadding(tft.width());
	SetScreenRotation(SystemInfo.nDisplayRotation);
	//ClearScreen();
	SetDisplayBrightness(SystemInfo.nDisplayBrightness);
	// see if the button is down, if so clear all settings
	if (!bWakeFromSleep && gpio_get_level((gpio_num_t)DIAL_BTN) == 0) {
		Preferences prefs;
		prefs.begin(prefsName);
		prefs.clear();
		prefs.end();
		WriteMessage("Factory Reset");
	}
	String msg;
	// see if we can read the settings
	if (SaveLoadSettings(false, true, false, true)) {
		if (!bWakeFromSleep && bAutoLoadSettings) {
			SaveLoadSettings(false, false, false, true);
			msg = "Settings Loaded";
		}
	}
	else {
#if TTGO_T == 1 || TTGO_T == 4
		// set the dial type
		CheckRotaryDialType();
#else
		// for the S3 MIW PCB we know the dial type
		SystemInfo.DialSettings.m_bToggleDial = true;
		SystemInfo.DialSettings.m_nDialPulseCount = 1;
#endif
		// see if there is a light sensor, read it until it is stable
		int lastVal = 0;
		int val = 0;
		for (int i = 0; i < 50; ++i) {
			val = ReadLightSensor();
			//Serial.println("read sensor: " + String(val));
			if (lastVal >= val)
				break;
			lastVal = val;
			delay(10);
		}
		SystemInfo.bHasLightSensor = val < 4094;
		// must not be anything there, so save it
		SaveLoadSettings(true, false, false, true);
	}
	// in case the saved ones were different
	SetScreenRotation(SystemInfo.nDisplayRotation);
	//ClearScreen();
	SetDisplayBrightness(SystemInfo.nDisplayBrightness);
	//WiFi
	if (SystemInfo.bRunWebServer) {
		WiFi.softAP(ssid, password);
		IPAddress myIP = WiFi.softAPIP();
		// save for the menu system
		strncpy(localIpAddress, myIP.toString().c_str(), sizeof(localIpAddress));
		Serial.print("AP IP address: ");
		Serial.println(myIP);
		server.begin();
		Serial.println("Server started");
		for (OnServerItem item : OnServerList) {
			server.on(item.path, item.function);
		}
		server.on("/fupload", HTTP_POST, []() { server.send(200); }, handleFileUpload);
		//server.on("/settings/increpeat", HTTP_GET, []() { server.send(200); }, IncRepeat);
		//server.on("/settings/increpeat", HTTP_GET, IncRepeat);
		/////////////////////////// End of Request commands
		server.begin();
	}
	if (bWakeFromSleep) {
		// see if we need to get the path back
		if (strlen(sleepFolder))
			currentFolder = sleepFolder;
	}
#if !HAS_BATTERY_LEVEL
	SystemInfo.bShowBatteryLevel = false;
#endif
	tft.setFreeFont(&Dialog_bold_16);
	tft.setTextColor(SystemInfo.menuTextColor);
	// get our text line sprite ready
	LineSprite.setColorDepth(16);
	LineSprite.createSprite(tft.width(), tft.fontHeight());
	LineSprite.fillSprite(TFT_BLACK);
	LineSprite.setFreeFont(&Dialog_bold_16);
	LineSprite.setTextPadding(tft.width());
	// get our Battery sprite ready
	BatterySprite.setColorDepth(16);
	BatterySprite.createSprite(100, tft.fontHeight() - 1 + BATTERY_BAR_HEIGHT);
	BatterySprite.fillSprite(TFT_BLACK);
	BatterySprite.setFreeFont(&Dialog_bold_16);
	BatterySprite.setTextPadding(tft.width());
	// get the file count sprite ready
	FileCountSprite.setColorDepth(16);
	FileCountSprite.createSprite(110, tft.fontHeight() + 2);
	FileCountSprite.fillSprite(TFT_BLACK);
	FileCountSprite.setFreeFont(&Dialog_bold_16);
	FileCountSprite.setTextPadding(tft.width());
	// get the menu system ready
	menuPtr = new MenuInfo;
	MenuStack.push(menuPtr);
	MenuStack.top()->menu = MainMenu;
	MenuStack.top()->index = 0;
	MenuStack.top()->offset = 0;
	leds = (CRGB*)calloc(LedInfo.nTotalLeds, sizeof(*leds));
	tmpLeds = (CRGB*)calloc(LedInfo.nTotalLeds, sizeof(*leds));
	if (LedInfo.bSwapControllers)
		FastLED.addLeds<NEOPIXEL, DATA_PIN2>(leds, 0, LedInfo.bSecondController ? LedInfo.nTotalLeds / 2 : LedInfo.nTotalLeds);
	else
		FastLED.addLeds<NEOPIXEL, DATA_PIN1>(leds, 0, LedInfo.bSecondController ? LedInfo.nTotalLeds / 2 : LedInfo.nTotalLeds);
	//FastLED.addLeds<NEOPIXEL, DATA_PIN2>(leds, 0, NUM_LEDS);	// to test parallel second strip
	// create the second led controller
	if (LedInfo.bSecondController) {
		if (LedInfo.bSwapControllers)
			FastLED.addLeds<NEOPIXEL, DATA_PIN1>(leds, LedInfo.nTotalLeds / 2, LedInfo.nTotalLeds / 2);
		else
			FastLED.addLeds<NEOPIXEL, DATA_PIN2>(leds, LedInfo.nTotalLeds / 2, LedInfo.nTotalLeds / 2);
	}
	FastLED.setTemperature(CRGB(LedInfo.whiteBalance.r, LedInfo.whiteBalance.g, LedInfo.whiteBalance.b));
	FastLED.setBrightness(LedInfo.nLEDBrightness);
	//FastLED.setMaxPowerInVoltsAndMilliamps(5, LedInfo.nPixelMaxCurrent);
	if (!bWakeFromSleep) {
		// this must run on same task as main or only the first few LEDs light using FastLED 3.5, don't know why, 3.3 worked
		xTaskCreatePinnedToCore(TaskInitTestLed, "LEDTEST", 10000, NULL, 1, &TaskLEDTest, xPortGetCoreID());
		if (SystemInfo.bRunArtNetDMX) {
			xTaskCreatePinnedToCore(TaskRunArtNet, "ARTNET", 10000, NULL, 1, &TaskArtNet, xPortGetCoreID());
		}
		tft.setTextColor(SystemInfo.menuTextColor);
		//grey_fill();
		rainbow_fill();
		tft.setTextColor(TFT_BLACK);
		tft.setFreeFont(&Irish_Grover_Regular_24);
		tft.drawRect(0, 0, tft.width() - 1, tft.height() - 1, SystemInfo.menuTextColor);
		tft.drawRect(1, 1, tft.width() - 2, tft.height() - 2, SystemInfo.menuTextColor);
#if TTGO_T == 1
		int nIndent = 0;
#else
		int nIndent = 40;
#endif
		tft.drawString("Magic Image Wand", 5 + nIndent, 10);
		tft.setFreeFont(&Dialog_bold_16);
		tft.drawString(String("Version ") + MIW_Version, 20 + nIndent, 70);
		tft.setTextSize(1);
		tft.drawString(__DATE__, 20 + nIndent, 90);
		if (msg.length()) {
			tft.drawString(msg, 20 + nIndent, 110);
		}
	}
	// clear the button buffer
	CRotaryDialButton::clear();
	// load the sleep timer
	sleepTimer = SystemInfo.nSleepTime * 60;
	GetFileNamesFromSDorBuiltins(currentFolder);
	// read the macro data
	if (bSdCardValid)
		ReadMacroInfo();
	for (int cnt = 0; cnt < 400; ++cnt) {
		if (ReadButton() != BTN_NONE) {
			break;
		}
		vTaskDelay(10 / portTICK_PERIOD_MS);
	}
	ClearScreen();
	DisplayCurrentFile();
	//// wait for led test to finish
	//eTaskState state = eTaskGetState(TaskLEDTest);
	//for (; state != eReady; delay(10)) {
	//	state = eTaskGetState(TaskLEDTest);
	//}
}

// task to run ArtNet
void TaskRunArtNet(void* parameter)
{
	artnet.setName(SystemInfo.cArtNetName);
	artnet.setNumPorts(1);
	artnet.enableDMXOutput(0);
	//artnet.disableDMXOutput(0);
	artnet.setStartingUniverse(SystemInfo.bStartUniverseOne ? 1 : 0);
	// use for ArtNetWiFi
	ConnectWifi();
	artnet.begin();
	// this will be called for each packet received
	artnet.setArtDmxCallback(onDmxFrame);
	while (true) {
		artnet.read();
		vTaskDelay(10 / portTICK_PERIOD_MS);
	}
}

// task to test the LEDS on start
void TaskInitTestLed(void* parameter)
{
	FastLED.clear(true);
	if (SystemInfo.bInitTest)
		TestLEDs(500);
	vTaskDelete(NULL);
}

// check and handle the rotary dial type
// if either A or B is 0, then this is a toggle dial
// else
// tell user to rotate one click
// delay
// if A or B is 0, then this is a toggle
// else it is a pulse dial
void CheckRotaryDialType()
{
	bool bA, bB;
	WriteMessage("checking dial type...", false, 1000);
	bA = gpio_get_level((gpio_num_t)DIAL_A);
	bB = gpio_get_level((gpio_num_t)DIAL_B);
	//Serial.println("ab " + String(bA) + String(bB));
	if (!bA && !bB) {
		// if both low must be a toggle
		SystemInfo.DialSettings.m_bToggleDial = true;
	}
	else {
		WriteMessage("Rotate dial 1 click", false, 10);
		// wait for rotate, they were both high before if we got this far, so just look at A
		while (gpio_get_level((gpio_num_t)DIAL_A))
			delay(10);
		// wait for button bounce
		delay(250);
		// read them again
		bA = gpio_get_level((gpio_num_t)DIAL_A);
		bB = gpio_get_level((gpio_num_t)DIAL_B);
		//Serial.println("ab " + String(bA) + String(bB));
		// if both low must be a toggle
		SystemInfo.DialSettings.m_bToggleDial = !bA && !bB;
		// we shouldn't need this again
	}
	if (!SystemInfo.DialSettings.m_bToggleDial)
		SystemInfo.DialSettings.m_nDialPulseCount = 2;
	WriteMessage(String("Dial Type: ") + (SystemInfo.DialSettings.m_bToggleDial ? "Toggle" : "Pulse"), false, 1000);
}

// read the macro info from the files if we didn't find the json file first
void ReadMacroInfo()
{
	if (SD_MIW.exists(MACRO_JSON_FILE)) {
		// read the file
#if USE_STANDARD_SD
		SDFile file;
		file = SD.open(MACRO_JSON_FILE);
		if (file) {
#else
		FsFile file;
		file = SD_MIW.open(MACRO_JSON_FILE);
		if (file.getError() == 0) {
#endif
		//WriteMessage("Reading: " + String(MACRO_JSON_FILE), false, 1000);
			JsonDocument doc;
			String input = file.readString();
			//Serial.println("json size: " + String(input.length()));
			DeserializationError err = deserializeJson(doc, input);
			if (err) {
				WriteMessage(String("failed to parse: ") + MACRO_JSON_FILE, true);
				//Serial.print(F("deserializeJson() failed with code "));
				//Serial.println(err.f_str());
			}
			else {
				// read the json into the macroinfo
				for (int ix = 0; ix < 10; ++ix) {
					MacroInfo[ix].description = String(doc[ix]["description"].as<const char*>());
					MacroInfo[ix].mSeconds = doc[ix]["mSeconds"];
					MacroInfo[ix].length = doc[ix]["length"].as<int>();
					MacroInfo[ix].pixels = doc[ix]["pixels"].as<int>();
					JsonArray ja = doc[ix]["images"];
					for (String str : ja) {
						MacroInfo[ix].fileNames.push_back(str);
					}
				}
			}
			file.close();
		}
		else {
#if USE_STANDARD_SD
			WriteMessage(String("failed to open: ") + MACRO_JSON_FILE, true);
#else
			WriteMessage(String("failed to open: ") + MACRO_JSON_FILE + " error: " + String(file.getError()), true);
#endif
		}
	}
	else {
		int fileCount, pixelWidth;
		WriteMessage(String("Creating: ") + MACRO_JSON_FILE, false, 1000);
		for (int ix = 0; ix < 10; ++ix) {
			String fn = MakeMIWFilename(String(ix), true);
			MacroInfo[ix].fileNames.clear();
			MacroInfo[ix].mSeconds = MacroTime("/" + fn, &fileCount, &pixelWidth, &MacroInfo[ix].fileNames);
			MacroInfo[ix].description = SD_MIW.exists("/" + fn) ? "Used" : "Empty";
			MacroInfo[ix].length = (float)pixelWidth / (float)LedInfo.nTotalLeds;
			MacroInfo[ix].pixels = pixelWidth;
		}
		// save the info since we just created it
		SaveMacroInfo();
	}
}
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
//void loop()
//{
//	int val1 = 0;
//	int val2 = 0;
//	int val3 = 0;
//	for (int i = 0; i < TWO_HUNDRED_PI; i++) {
//		val1 = round(255 / 2.0 * (sin(i / 100.0) + 1));
//		val2 = round(255 / 2.0 * (sin(i / 100.0 + TWO_THIRDS_PI) + 1));
//		val3 = round(255 / 2.0 * (sin(i / 100.0 - TWO_THIRDS_PI) + 1));
//
//		leds[7] = CHSV(0, 255, val1);
//		leds[8] = CHSV(96, 255, val2);
//		leds[9] = CHSV(160, 255, val3);
//
//		FastLED.show();
//
//		delay(1);
//	}
//}

// #########################################################################
// Fill screen with a rainbow pattern
// #########################################################################
void rainbow_fill()
{
	byte red = 31;
	byte green = 0;
	byte blue = 0;
	byte state = 0;
	unsigned int color = red << 11; // Colour order is RGB 5+6+5 bits each
	// The colours and state are not initialised so the start colour changes each time the function is called

	for (int i = tft.height() - 1; i >= 0; i--) {
		// Draw a vertical line 1 pixel wide in the selected colour
		tft.drawFastHLine(0, i, tft.width(), color); // in this example tft.width() returns the pixel width of the display
		// This is a "state machine" that ramps up/down the colour brightnesses in sequence
		switch (state) {
		case 0:
			green++;
			if (green == 64) {
				green = 63;
				state = 1;
			}
			break;
		case 1:
			red--;
			if (red == 255) {
				red = 0;
				state = 2;
			}
			break;
		case 2:
			blue++;
			if (blue == 32) {
				blue = 31;
				state = 3;
			}
			break;
		case 3:
			green--;
			if (green == 255) {
				green = 0;
				state = 4;
			}
			break;
		case 4:
			red++;
			if (red == 32) {
				red = 31;
				state = 5;
			}
			break;
		case 5:
			blue--;
			if (blue == 255) {
				blue = 0;
				state = 0;
			}
			break;
		}
		color = red << 11 | green << 5 | blue;
	}
}

//// fill the screen with grey
//void grey_fill()
//{
//	//for (int ix = 0; ix < tft.width(); ++ix) {
//	//	if (ix % 2)
//	//		tft.drawFastVLine(ix, 0, tft.height(), TFT_LIGHTGREY);
//	//	else
//	//		tft.drawFastVLine(ix + 1, 0, tft.height(), TFT_DARKGREY);
//	//}
//	tft.fillRect(0, 0, tft.width(), tft.height(), TFT_DARKGREY);
//}

// draw a progress bar
void DrawProgressBar(int x, int y, int dx, int dy, int percent, bool rect)
{
	if (rect)
		tft.drawRoundRect(x, y, dx, dy, 2, SystemInfo.menuTextColor);
	int fill = (dx - 2) * percent / 100;
	// fill the filled part
	tft.fillRect(x + 1, y + 1, fill, dy - 2, TFT_DARKGREEN);
	// blank the empty part
	tft.fillRect(x + 1 + fill, y + 1, dx - 2 - fill, dy - 2, TFT_BLACK);
}

// save/load settings
// return false if not found or wrong version
bool SaveLoadSettings(bool save, bool autoloadonly, bool ledonly, bool nodisplay)
{
	bool retvalue = true;
	Preferences prefs;
	prefs.begin(prefsName, !save);
	if (save) {
		//Serial.println("saving");
		prefs.putString(prefsVersion, MIW_Version);
		prefs.putBool(prefsAutoload, bAutoLoadSettings);
		// save things
		if (!ledonly) {
			prefs.putBytes(prefsImgInfo, &ImgInfo, sizeof(ImgInfo));
			prefs.putBytes(prefsBuiltInInfo, &BuiltinInfo, sizeof(BuiltinInfo));
			if (!nodisplay)
				WriteMessage("Settings Saved", false, 500);
		}
		// we always do these since they are hardware related
		prefs.putBytes(prefsLedInfo, &LedInfo, sizeof(LedInfo));
		prefs.putBytes(prefsSystemInfo, &SystemInfo, sizeof(SystemInfo));
		prefs.putBytes(prefsBuiltinInfo, &BuiltinInfo, sizeof(BuiltinInfo));
	}
	else {
		// load things
		String vsn = prefs.getString(prefsVersion, "");
		if (vsn == MIW_Version) {
			if (autoloadonly) {
				bAutoLoadSettings = prefs.getBool(prefsAutoload, false);
				//Serial.println("getting autoload: " + String(bAutoLoadSettings));
			}
			else if (!ledonly) {
				prefs.getBytes(prefsImgInfo, &ImgInfo, sizeof(ImgInfo));
				prefs.getBytes(prefsBuiltInInfo, &BuiltinInfo, sizeof(BuiltinInfo));
				int savedFileIndex = currentFileIndex.nFileIndex;
				// we don't know the folder path, so just reset the folder level
				currentFolder = "/";
				setupSDcard();
				GetFileNamesFromSDorBuiltins(currentFolder);
				currentFileIndex.nFileIndex = savedFileIndex;
				// make sure file index isn't too big
				if (currentFileIndex.nFileIndex >= FileNames.size()) {
					currentFileIndex.nFileIndex = 0;
				}
				// set the brightness values since they might have changed
				SetDisplayBrightness(SystemInfo.nDisplayBrightness);
				if (!nodisplay)
					WriteMessage("Settings Loaded", false, 500);
			}
			// these are always done
			prefs.getBytes(prefsLedInfo, &LedInfo, sizeof(LedInfo));
			prefs.getBytes(prefsSystemInfo, &SystemInfo, sizeof(SystemInfo));
			prefs.getBytes(prefsBuiltinInfo, &BuiltinInfo, sizeof(BuiltinInfo));
		}
		else {
			retvalue = false;
			if (!nodisplay)
				WriteMessage("Settings not saved yet", true, 2000);
		}
	}
	prefs.end();
	return retvalue;
}

// delete saved settings
void FactorySettings(MenuItem* menu)
{
	if (GetYesNo("Reset All Settings? (reboot)")) {
		Preferences prefs;
		prefs.begin(prefsName);
		prefs.clear();
		prefs.end();
		ESP.restart();
	}
}

void EraseFlash(MenuItem* menu)
{
	if (GetYesNo("Format EEPROM? (factory reset)")) {
		nvs_flash_erase(); // erase the NVS partition and...
		nvs_flash_init(); // initialize the NVS partition.
		//SaveLoadSettings(true);
	}
}

void ReportCouldNotCreateFile(String target) {
	SendHTML_Header();
	webpage += F("<h3>Could Not Create Uploaded File (write-protected?)</h3>");
	webpage += F("<a href='/"); webpage += target + "'>[Back]</a><br><br>";
	append_page_footer();
	SendHTML_Content();
	SendHTML_Stop();
}

#if USE_STANDARD_SD
SDFile UploadFile;
#else
FsFile UploadFile;
#endif

// upload a new file to the Filing system
void handleFileUpload()
{
	HTTPUpload& uploadfile = server.upload(); // See https://github.com/esp8266/Arduino/tree/master/libraries/ESP8266WebServer/srcv
											  // For further information on 'status' structure, there are other reasons such as a failed transfer that could be used
	if (uploadfile.status == UPLOAD_FILE_START)	{
		String filename = uploadfile.filename;
		String filepath = String("/");
		if (!filename.startsWith("/"))
			filename = "/" + filename;
		//Serial.print("Upload File Name: " + filename);
		SD_MIW.remove(filename);   // Remove a previous version just to start clean
#if USE_STANDARD_SD
		UploadFile = SD.open(filename, FILE_WRITE);  // Open the file for writing in SPIFFS (create it, if doesn't exist)
#else
		UploadFile = SD_MIW.open(filename, O_WRITE | O_CREAT);
#endif
		filename = String();
	}
	else if (uploadfile.status == UPLOAD_FILE_WRITE)
	{
		if (UploadFile)
			UploadFile.write(uploadfile.buf, uploadfile.currentSize); // Write the received bytes to the file
	}
	else if (uploadfile.status == UPLOAD_FILE_END)
	{
		if (UploadFile)          // If the file was successfully created
		{
			UploadFile.close();   // Close the file again
			//Serial.print("Upload Size: "); Serial.println(uploadfile.totalSize);
			webpage = "";
			load_page_header(false);
			webpage += F("<h3>File was successfully uploaded</h3>");
			webpage += F("<h2>Uploaded File Name: "); webpage += uploadfile.filename + "</h2>";
			webpage += F("<h2>File Size: "); webpage += file_size(uploadfile.totalSize) + "</h2><br>";
			append_page_footer();
			server.send(200, "text/html", webpage);
			// reload the file list, if not showing built-ins
			if (!ImgInfo.bShowBuiltInTests) {
				GetFileNamesFromSDorBuiltins(currentFolder);
			}
		}
		else
		{
			ReportCouldNotCreateFile("upload");
		}
	}
}
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

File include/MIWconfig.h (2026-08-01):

#pragma once
// ***** Various switches for options are set here *****

// use TTGO_T 1, 3 or 4, uncomment only one of these
//#define TTGO_T 1
// choose TTGO T-Display for compile type (or T1 if that doesn't work)
// ****** this is now defined in the platformio.ini file for each build environment ******
// #define TTGO_T 3	// for S3 chip
// choose LilyGo T-Display S3 for compile type
//#define TTGO_T 4
// choose LilyGo T4 for compile type

// **** NOTE ****
// If you compile for TTGO 1 and load on S3 the S3 will not run and the boot loader will be disabled
// To fix this: Press and hold the BOOT button, press and release reset, and then release BOOT.
// Upload the firmware and then press the reset button. After this all will function normally again.

// also remember to change User_Setup_Select.h correctly
// use one of these in that file
//#include <User_Setups/Setup25_TTGO_T_Display.h>    // Setup file for ESP32 and TTGO T-Display ST7789V SPI bus TFT
//#include <User_Setups/Setup206_LilyGo_T_Display_S3.h>     // For the LilyGo T-Display S3 based ESP32S3 with ST7789 170 x 320 TFT
//#include <User_Setups/Setup22_TTGO_T4.h>           // Setup file for ESP32 and TTGO T4 version 1.2
//#include <User_Setups/Setup22_TTGO_T4_v1.3.h>      // Setup file for ESP32 and TTGO T4 version 1.3
// make sure this one is commented out
//#include <User_Setup.h>           // Default setup is root library folder

// 1 for standard SD library, 0 for the new exFat library which allows > 32GB SD cards
#define USE_STANDARD_SD 0

#if TTGO_T == 1
	// onboard buttons
	#define ONBBTN0 GPIO_NUM_0
	#define ONBBTN1 GPIO_NUM_35
	// TFT PWM control pin
	#define TFT_PWM_PIN 4
	// SD details
	#define SDcsPin    33  // GPIO33
	#define SDSckPin   25  // GIPO25
	#define SDMisoPin  27  // GPIO27
	#define SDMosiPin  26  // GPIO26
	// LED controller pins
	#define DATA_PIN1 2
	#define DATA_PIN2 17
	// battery level
	#define HAS_BATTERY_LEVEL 1
	// the wheel frame advance gpio port
	#define FRAMEBUTTON_GPIO 32
	// battery sensor GPIO
	#define BATTERY_SENSOR_GPIO 36
	// the optional light sensor GPIO to control the LCD brightness
	#define LIGHT_SENSOR_GPIO 39
	// The push button setting, set to 1 for onboard PS version 1.4 (NOTE: PCB not ever created)
	#if 0
		#define DIAL_BTN 37
	#else
		#define DIAL_BTN 15
	#endif
	// default dial direction GPIO ports
	#define DIAL_A 13
	#define DIAL_B 12
#elif TTGO_T == 3
	// onboard buttons
	#define ONBBTN0 GPIO_NUM_0
	#define ONBBTN1 GPIO_NUM_14
	// TFT PWM control pin
	#define TFT_PWM_PIN 38
	// SD details
	#define SDcsPin    10
	#define SDSckPin   12
	#define SDMisoPin  11
	#define SDMosiPin  13
	// LED controller pins
	#define DATA_PIN1 21
	#define DATA_PIN2 16
	// battery level
	#define HAS_BATTERY_LEVEL 1
	// the wheel frame advance gpio port
	#define FRAMEBUTTON_GPIO 18
	// battery sensor GPIO
	#define BATTERY_SENSOR_GPIO 4
	// the optional light sensor GPIO to control the LCD brightness
	#define LIGHT_SENSOR_GPIO 17
	// set the push button GPIO port
	#define DIAL_BTN 3
	#define DIAL_A 1
	#define DIAL_B 2
#elif TTGO_T == 4
	// onboard buttons
	#define ONBBTN0 GPIO_NUM_0
	#define ONBBTN1 GPIO_NUM_35
	// TFT PWM control pin
	#define TFT_PWM_PIN 4
	// SD details
	#define SDcsPin    13
	#define SDSckPin   14
	#define SDMisoPin  2
	#define SDMosiPin  15
	// LED controller pins
	#define DATA_PIN1 19
	#define DATA_PIN2 25
	// battery level
	#define HAS_BATTERY_LEVEL 0
	// the wheel frame advance gpio port
	#define FRAMEBUTTON_GPIO 0
	// battery sensor GPIO
	#define BATTERY_SENSOR_GPIO 34
	// the optional light sensor GPIO to control the LCD brightness
	#define LIGHT_SENSOR_GPIO 35
	// set the push button GPIO port
	#define DIAL_BTN 37
	#define DIAL_A -1
	#define DIAL_B -1
#endif

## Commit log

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2020-12-19 Limping now, fixed many display issues but still needs work. bmp files not working yet.
    [MagicImageWand.h]
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2020-12-20 BMP preview not working, this is just to save the code.
    [MagicImageWand.h]
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2020-12-22 Fixed playback of BMP files with names longer than 14 characters.
    [MagicImageWand.h]
2020-12-22 Removed invert display. Useless option.
    [MagicImageWand.h]
2020-12-22 Fixed display brightness control and progress bar when entering integers.
    [MagicImageWand.h]
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2020-12-26 Larger font and some shortened menu items. Easier to read the display.
    [MagicImageWand.h]
2020-12-26 Show IP address in main menu. Fixed the integer entry, it was clipping the text above the progress bar.
    [MagicImageWand.h]
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2020-12-31 replaced f3d with complete assembly
    [MagicImageWandCase.f3d, MagicImageWandCase.f3z]
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2021-02-13 Added button 35 as long press. Fixed display of macro #.
    [MagicImageWand.h]
2021-02-14 Added menu to select LED wiring mode. 0 is lower reversed, upper normal 1 is lower and upper normal, chained in middle. 2 is lower normal, and top reversed, no connection in middle, this allows LED i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
    [MagicImageWand.h]
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2021-02-14 Added menu entry to show BMP size. Fixed bug not closing file after preview.
    [MagicImageWand.h, RotaryDialButton.h]
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2021-02-26 Added setting for max LED milliamps. Also started adding LED count to lightbar, not working yet.
    [MagicImageWand.h]
2021-03-23 Made all error messages red. Fixed some startup code.
    [MagicImageWand.h]
2021-03-30 Changed the menu active line to be reverse video of the other lines.
    [MagicImageWand.h]
2021-03-30 Moved progress bar to line 1 and made current file reverse video to be consistent with the new menus.
    [MagicImageWand.h]
2021-04-01 Added option to control * or reverse video for menu selection and reverse video on or off for current file.
    [MagicImageWand.h]
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2021-04-04 Fixed image preview, it was redrawing constantly. That's why the button was sometimes ignored. This also has some of the code to handle 288 tall BMP files. Almost working correctly, sideways scrollin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
    [MagicImageWand.h]
2021-04-04 Fixed 288 pixel preview.
    [MagicImageWand.h]
2021-04-04 Removed reverse dial and preview scroll from the MIW commands. They are system commands and don't belong in the MIW files.
    [MagicImageWand.h]
2021-04-12 Fixed sub sub ... folder navigation when moving back up to parents.
    [MagicImageWand.h]
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2021-04-12 Fixed total leds menu entry. %s -> %d. Crash.
    [MagicImageWand.h]
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2021-04-13 Fixed light bar to handle more pixels.
    [MagicImageWand.h]
2021-04-13 Added a warning message about rebooting when changing the pixel count or controllers.
    [MagicImageWand.h]
2021-04-13 Made controller and LED count changes always force a reboot. We had to do this since the fastled library does not allow changing the buffer size at runtime.
    [MagicImageWand.h]
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2021-04-28 Experiment to fix the switch error some people are seeing.
    [MagicImageWand.h]
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2021-05-07 Made preview dial move in direction of moving the image, that is reverse from what it was, but it seems more intuitive.
    [MagicImageWand.h]
2021-05-11 SettingsSaveRestore() was not calculating the correct number of bytes to allocate. Could cause a crash.
    [MagicImageWand.h]
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2021-05-21 Started adding code to handle sideways menu scrolling. Also fixed a possible bug with displaymenuline being called with negative line numbers.
    [MagicImageWand.h]
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2021-05-23 Improved sideways scroll with adjustable pauses on each end and reverse speed multiplier.
    [MagicImageWand.h]
2021-05-23 Minor menu text changes. Fixed show BMP during running with progress bar so it looks better.
    [MagicImageWand.h]
2021-05-24 Improved display while running for 288 pixel images. Might still have some bugs.
    [MagicImageWand.h]
2021-05-25 Added confirmation screen before erasing or resetting or formatting eeprom.
    [MagicImageWand.h]
2021-05-27 Fixed rainbow pulse to use the highest pixel. Added experimental battery level reading code.
    [MagicImageWand.h]
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2021-05-27 Fixed battery menu text, % should have been %%.
    [MagicImageWand.h]
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2021-06-03 Moved bshowbuiltin to imginfo. It was originally in systeminfo, but since that is always loaded now it resulted in odd behavior: Rebooting after selecting builtin would show the SD files, but it woul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
    [MagicImageWand.h]
2021-06-04 Fixed a bug where folders wouldn't display after wakeup from sleep.
    [MagicImageWand.h]
2021-06-04 Fixed the code to restore the current folder and file selection after sleeping. Note that SystemInfo and LedInfo are always loaded, it doesn't matter if it was cold boot or from sleep.
    [MagicImageWand.h]
2021-06-05 The system menu was getting too big, so I moved some things to submenus. I hope this is more organized now. New features: 1. Display timeout that dims the LCD. 2. Optional sleep timer to sleep after 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
    [MagicImageWand.h]
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2021-06-06 Improved handling of reboot when LED controller setting changed.
    [MagicImageWand.h]
2021-06-07 Improved menu text. Fixed step size display when entering decimal values. Modified folder display so that when it is off,it will still show the parent in front of the < character.
    [MagicImageWand.h]
2021-06-08 Fixed the lightbar that was broken with the last checkin.
    [MagicImageWand.h]
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2021-06-17 Menu changes. Nesting of eIfEqual/eEndif is now allowed, it didn't work before. There are two menu systems now. Full and simple. The simple one is much smaller and only has a few common settings.
    [MagicImageWand.h]
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2021-06-23 Fixed an off by 1 problem when displaying the letters for selecting name filter.
    [MagicImageWand.h]
2021-06-24 Changed the name filter characters to reverse video for the selected character. When menu star is selected instead of hilite then the selected character will be displayed in white. Long press btn0 cl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
    [MagicImageWand.h]
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2021-07-11 Fix for new battery voltage checking values, wil change again when the latest PCB's are tested. Made changes to the LightBar. It now has a delay mode that will slow the transition of HUE when rotatin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
    [MagicImageWand.h]
2021-07-12 Fixed the brightness control for the Kelvin lightbar mode. It was blasting light at 100% and often causing a reset.
    [MagicImageWand.h]
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2021-07-16 Fixed the lightbar display to show the correct increment value after each run. It was staying at 1 even when it shouldn't be.
    [MagicImageWand.h]
2021-07-17 Fixed pixel count left rotate dial using slow change in the lightbar. It was getting stuck at 1 pixel.
    [MagicImageWand.h]
2021-07-20 Fixed bug where built-in preview would only show the first time.
    [MagicImageWand.h]
2021-07-20 Fixed another case where the cancel flag wasn't being reset and it stopped the preview. This happened after running a built-in and stopping it with long press.
    [MagicImageWand.h]
2021-07-21 Fixed the repeat pause message, the line wasn't being cleared between repeats.
    [MagicImageWand.h]
2021-07-23 Fixed the interrupt code so the false clicksthat sometimes happened with rotation get stopped.
    [MagicImageWand.h, RotaryDialButton.h]
2021-07-23 Revert "Fixed the interrupt code so the false clicksthat sometimes happened with rotation get stopped."
    This reverts commit e0bb9c3a80a2aa190375f503468fca06edacc257.
    [MagicImageWand.h, RotaryDialButton.h]
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2021-07-23 Really fixed the interrupt problem that was causing false clicks on dial rotation sometimes on the new PCB.
    [RotaryDialButton.h]
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2021-08-08 Corrected frame button to 32, 22 was really old version.
    [MagicImageWand.h]
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2021-08-23 Improved rotary switch reading, needed 2mS debounce, 1mS not quite enough, sometimes it would read the wrong direction.
    [RotaryDialButton.h]
2021-08-23 Fixed a bug when showing macro information with more than 7 files in it. It wasn't scrolling correctly.
    [MagicImageWand.h, RotaryDialButton.h]
2021-08-25 BMP was checking for img_size != 0 and flagging it as a zero if it was 0. The spec actually allows 0, so some rare BMP files would fail even though they were ok. This is now fixed, that field wasn't 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
    [MagicImageWand.h]
2021-08-26 Corrected battery levels from testing with latest PCB's.
    [MagicImageWand.h]
2021-08-28 Added a pulse/toggle setting to the dial settings. The older PCB dial sent pulses while the newer one toggles. This resulted in erratic operation of the older PCB. The new one will now take two click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
    [MagicImageWand.h, RotaryDialButton.h]
2021-08-29 Added a description (text) to each macro. The information is now held in /macros.json. Everybody please test and let me know if you find any issues with the json file getting out of sync with the act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
    [MagicImageWand.h]
2021-08-29 Added automatic setting of the rotary dial type. You might be asked to rotate it one click. It doesn't work as well with the rotary dials without the click. It is only done once after a factory reset.
    [MagicImageWand.h]
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2021-08-30 Fixed the built-ins using random pixel address, it could generate addresses that was out of range, the max index should have been ledcount-1.
    [MagicImageWand.h]
2021-09-01 Added code to show total macro time on the display during macro running. It isn't very accurate yet, that could use some improvement. There might be some problems with the macro repeat display that h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
    [MagicImageWand.h]
2021-09-02 Improved the timing display of macros. Fixed a bug that was looking in the wrong folder for the macro files when the default folder is not /.
    [MagicImageWand.h]
2021-09-02 Added code to fix the "MACRO TIME" from older macro (.MIW) files. The time was in seconds, for better resolution it is now in mSec.
    [MagicImageWand.h]
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2021-09-05 Added an option to sleep if the battery is too low. DO NOT enable this if you don't have the battery connected. If you do this you will have to do a factory reset in order to boot properly again. Thi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
    [MagicImageWand.h]
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2021-09-06 Fixed macro display when 0 files in the macro. Allow click to edit description from macro information display. Highlight description to emphasize that it is editable from click.
    [MagicImageWand.h]
2021-09-07 Removed the max current setting. It doesn't actually work well, it was just another way of limiting the brightness of the pixels. I changed "Brightness" to "Max Brightness" in the menus to better ref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
    [MagicImageWand.h, RotaryDialButton.h]
2021-09-07 Fixed a bug in the sleep on low power that making it trigger on boot, the AD converter wasn't stable yet.
    [MagicImageWand.h]
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2021-09-08 Added a few more B0/B1 button functions. During integer entry long B0 resets the value and B0 toggles the increment amount. Also added earlier was during menu: B0 goes up one level. Long B0 goes to t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
    [MagicImageWand.h]
2021-09-08 Pressing both B0 and B1 for long press time will cause a system reset, unless the system is really crashed! Updated the docx file.
    [MagicImageWand.h]
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2021-09-14 Fixed handle joiner lengths
    [18650 Dual Battery Handle Builtin PS V2 v11.f3d, Joiner.3mf]
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2021-09-20 Fixed code to remove some compiler warnings
    [MagicImageWand.h]
2021-09-20 Fixed '0x7e' to '\x7e'. Modified simple menu macro to be a submenu and added info to it so we can get the walk time and distance.
    [MagicImageWand.h]
2021-09-23 Fixed lightbar help text for inc/dec delay setting.
    [MagicImageWand.h]
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2021-10-03 When changing dimming modes, set the display correctly when not sensor mode.
    [MagicImageWand.h]
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2021-10-06 Fixed a bug that made the rotary dial act very strange. Ints could be left off when rotated too tast.
    [MagicImageWand.h, RotaryDialButton.h]
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2021-10-10 Improved 3D printing versions. Better tolerances on the battery end cap.
    [18650 Dual Battery Handle Builtin PS V2 v23.f3d, 18650 Dual Battery Handle Builtin PS V2 v28.f3d, 18650end.3mf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]
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2021-10-12 FIxed strange button behaviour when rotating dial while showing preview information. This happened for image that could scroll sideways. The display would sometimes go back to the bmp and sometimes n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
    [MagicImageWand.h]
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2021-10-15 Made bezel bigger to handle tolerances between TTGO chips from different vendors.
    [MIW with PS TTGO Case v45.f3z, MIW with PS TTGO Case v48.f3z, MIWPS Bottom.3mf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]
2021-10-15 Fixed a pixel wrapping problem with the sine pattern and the beats pattern. One pixel was wrapping to the other end of the LEDs.
    [MagicImageWand.h]
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2021-12-25 Fixed the battery % display to update correctly.
    [MagicImageWand.h]
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2021-12-26 Fixed image file scrolling so it is pinned to images and hitting a folder won't exit. Also cleaned up some of the code if a bmp is bad.
    [MagicImageWand.h]
2021-12-26 Fixed blinking screen when viewing images that happened when dial rotated left at first image in folder. Made the preview scroll mode sticky so it remembers which mode was used last time.
    [MagicImageWand.h]
2021-12-27 Fixed the sleep on low battery so it should work with no battery connected. The minimum raw value must be at least 900 which will be true with even a very low battery connected.
    [MagicImageWand.h]
2021-12-27 Undid the changes to improve the rotary dial reading. It broke the btn reading of long presses.
    [MagicImageWand.h, RotaryDialButton.h]
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2021-12-27 Added a new setting for the starting offset of the preview display. This was fixed at 5 before which removed the top 5 and the bottom 4 rows of the image so that the 144 pixels would fit in the 135 p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
    [MagicImageWand.h]
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2021-12-30 Improved dial interrupt code. But there is still a problem that happens sometimes after preview and rapidly rotating the dial where the button code goes crazy and doesn't return the correct buttons u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
    [MagicImageWand.h, RotaryDialButton.h]
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2021-12-31 Update BOM etc for 1.2 PCB. C10 had wrong mfg part number.
    [BOM_TTGO MIW PCB_2021-08-04.csv, PickAndPlace_TTGO MIW PCB_2021-08-04.csv]
2021-12-31 Make some changes that seem to improve the rapidly rotating dial issue, but it is still there, just harder to cause.
    [MagicImageWand.h, RotaryDialButton.h]
2022-01-01 Fixed image preview so it ignores the display timeout value. The display was dimming while previewing, there doesn't seem to be any reason for that.
    [MagicImageWand.h]
2022-01-01 Made it harder to crash with really fast dial rotation but it still happens. Still don't know the exact reason though. Puzzling problem.
    [MagicImageWand.h, RotaryDialButton.h]
2022-01-02 More improvements to the rotary dial code. It is getting harder to duplicate the problem with rotating the dial really fast. It still happens but not very often.
    [MagicImageWand.h, RotaryDialButton.h]
2022-01-02 Fixed the built-in lines pattern so it clears reliably after long press.
    [MagicImageWand.h]
2022-01-02 Fixed the one dot built-in so it properly clears after a long press.
    [MagicImageWand.h]
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2022-01-19 Improved the rotary dial reading, it would sometimes go the wrong direction.
    [MagicImageWand.h, RotaryDialButton.h]
2022-01-19 Fixed the files in MIWPS1_2 to be correct.
    [BOM_TTGO MIW PCB UNIFIED_2022-01-19.csv, BOM_TTGO MIW PCB_2021-08-04.csv, PickAndPlace_TTGO MIW PCB UNIFIED_2022-01-19.csv]
2022-01-20 FIxed the broken long press from the previous version.
    [MagicImageWand.h, RotaryDialButton.h]
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2022-01-23 Added esp32encoder library to handle the rotating dial, it is much better than my code, it works reliably! I haven't seen any problems reading the dial now. Removed the dial delay and acceleration op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
    [MIWconfig.h, MagicImageWand.h, RotaryDialButton.h]
2022-01-27 FIxed the preview for 288 pixel bitmaps. Also fixed the sideways scrolling display during preview showing the image stats.
    [MagicImageWand.h]
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2022-02-14 Fixed the flashing cursor when naming macros. The screen was being redrawn continuously!
    [MagicImageWand.h]
2022-02-20 Improved the display during scrolling of image files. The folder doesn't appear and disappear as the cursor is moved. Added BTN0 long as help. Only a few lines have help so far, but more will be adde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
    [MagicImageWand.h]
2022-02-20 Improved the help message handler so that newlines are added automatically to prevent words being split across line boundaries.
    [MagicImageWand.h]
2022-02-21 Fixed the case design for the latest PCB without power supply (voltage regulator). This is in the 5A version but can be used for the older 3A design also.
    [SB CPU Case TTGO v38.f3d, SB CPU Case TTGO v40.f3d, TTGO Top.3mf]
2022-02-21 Shortened bezel on 5A model to avoid hitting the LCD.
    [SB CPU Case TTGO v40.f3d, SB CPU Case TTGO v41.f3d, TTGO Top.3mf]
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2022-03-28 Fixed the problem with built-ins that ignore changes to the frame hold time.
    [MagicImageWand.h]
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2022-04-02 Fixed builtin disc display when sizes less than full strip are used. Centered the disc.
    [MagicImageWand.h]
2022-04-02 Renamed disc buitlin to circles. Added a count and gap between repetitions. Made the builtin settings "sticky" so they changes remain after rebooting, just like system settings.
    [MagicImageWand.h]
2022-04-02 Fixed the gap when less than full size circles used in the builtins. Also change the menu to say "circles" instead of "disc".
    [MagicImageWand.h]
2022-07-16 Added TTGO T4 support during compile. Still has a few bugs, but mostly works. It crashes after image preview, don't know why yet.
    [MIWconfig.h, MagicImageWand.h, RotaryDialButton.h]
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2022-08-23 Switched back to standard SD library to work better with WebServer. Also fixed the code to compile with sdFat again by extending WebServer to handle the .getName(). Haven't tested this yet though. St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
    [MIWconfig.h, MagicImageWand.h]
2022-08-23 Added base class initializer to WebServerX. Also fixed the path to WebServer.h in WebServerX.h.
    [MagicImageWand.h]
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2022-09-07 Force a reboot when any ArtNet changes are made.
    [MagicImageWand.h]
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2022-09-14 Fixed the webpage file upload, accidentally broken during editing. Added some code to show the files on the home page, a future revision will allow changing the current file from the webpage.
    [MagicImageWand.h]
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2022-09-15 Fixed drop down file list to handle folders as well as files.
    [MagicImageWand.h]
2022-09-16 Compiled with FastLED 3.3.3, later versions like 3.4 do not work correctly for an unknown reason, only the first 5 led's light.
    [MagicImageWand.h]
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2022-09-24 Fixed the problem with running the latest version of the FastLED library. It now works. For some unknown reason versions 3.4 and later did not like the LED test code running from a task pinned to cor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
    [MagicImageWand.h]
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2022-10-03 Put a "Select Folder" button back on the home page. The onchange event doesn't happen when you click on the already selected folder, which makes folder navigation harder, you have to select a file fi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
    [MagicImageWand.h]
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2022-10-04 Fixed some web server run macro issues. It would hang or simply not stop playing sometimes.
    [MagicImageWand.h]
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2022-10-06 Fixed a problem on the web settings page that wasn't handling checkboxes correctly.
    [MagicImageWand.h]
2022-10-07 On the settings server page, moved the image chain options up to the image settings section. It didn't really belong in the repeat section.
    [MagicImageWand.h]
2022-10-15 Added ability to swap the L1/L2 controllers. Also fixed a bug in ToggleBool() that was calling menu change handlers with -1, it should have been 0.
    [MagicImageWand.h]
2022-10-17 Fixed preview bug when LED pixels less than bmp pixels. e.g. 142/144.
    [MagicImageWand.h]
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2022-10-20 Fixed menu to html code to handle nested menu if/else/endif blocks. Improved the display of checkboxes so they show the choices text.
    [MagicImageWand.h]
2023-03-13 Removed serial2 init that caused reading uSD card to fail.
    [MagicImageWand.h]
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2023-07-10 FIxed a constant to 64 bits to avoid compiler warning message.
    [18650RotatorHandle.3mf]
2023-08-24 Added upside down option to simple menu. FIxed bmp preview to honor the upside down flag.
    [MagicImageWand.h]
2023-08-31 Fixed the walk to left/right setting to work correctly with 180 rotated images.
    [MagicImageWand.h]
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2023-10-21 Fixed display, the file count was showing when menus were displayed, it messed up the last menu line.
    [MagicImageWand.h]
2023-11-01 Changed column menu items to "crop". It makes more sense. Moved the "reset crop on change" to the system preview menu.
    [MagicImageWand.h]
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2023-11-07 FIxed scrolling issue when moving the right crop mark past the left of the display.
    [MagicImageWand.h]
2023-11-08 Fixed some display problems with the crop bars. Made the active dial crop mark green.
    [MagicImageWand.h]
2023-11-08 Switching from left crop to right crop didn't make it visible if it was hidden. It was 1 column off. Only reset the crop marks when they have not been set yet. They were getting reset to the left and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
    [MagicImageWand.h]
2023-11-08 Fixed crash when trying to edit crop lines that are both scrolled off the screen.
    [MagicImageWand.h]
2023-11-09 FIxed more display issues with crop editing. Fixed long B0 so it moves the image up and down again.
    [MagicImageWand.h]
2023-11-09 Fixed display problem hitting B1 and the crop was close to the beginning, garbage would display on the left. Also fixed the bug that prevented images shorter than 240 pixels from displaying.
    [MagicImageWand.h]
2023-11-11 Change B1+Dial to reboot. This replaces B0+B1. Added B0+B1 to reset crop marks.
    [MagicImageWand.h, RotaryDialButton.h]
2023-11-11 Don't show crop marks if the size is showing. Fixed selection * display when not using color bar.
    [MagicImageWand.h]
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2023-12-02 Made DisplayLine color args uint16_t which is more correct.
    [MagicImageWand.h]
2023-12-05 Fixed the flicker in the integer bar graph while entering date. It was being redrawn too fast, now it is drawn only when changed. Changed the top line to show the original value, not the new one, sin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
    [MagicImageWand.h]
2023-12-07 Fixed a problem when browsing images in preview mode. Once an 8-bit image was displayed the 24-bit ones would not display correctly. This was caused by not freeing the color table.
    [MagicImageWand.h]
2023-12-12 Fixed left and right crop in macro files so they precede the image display! Added a macro setting to wait for a key before continuing to the next file.
    [MagicImageWand.h]
2023-12-15 Fixed some 8 bit images, the color table was set to 0 meaning 256. Added scaling when images greater than 144(or 288 with two strips). Done to handle PixelStick 200 pixel images.
    [MagicImageWand.h]
2023-12-15 Fixed the distance walking when the image height has been scaled due to being more than 144 pixels. If the height is reduced then the walking distance must also be reduced.
    [MagicImageWand.h]
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2024-01-24 Fixed value of BTN1 for S3 chip. Incremented the version number. Please remember to set the correct TTGO in the MIWconfig.h file.
    [MIWconfig.h, MagicImageWand.h]
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2024-01-27 Fixed the battery levels for the S3, and removed the battery count menu setting. Added GPIO15 port enable to turn the backlight on when running on battery.
    [MIWconfig.h, MagicImageWand.h]
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2024-04-12 Fixed display dim timer that was broken in 3.18.
    [MagicImageWand.h]
2024-04-15 Fixed to compile with latest esp32Encoder (10.5 I think). Tried to fix S3 issue with restart after sleep. Not quite working yet, might be S3 issue, RTC data is not preserved.
    [MIWconfig.h, RotaryDialButton.h]
2024-04-15 More slight changes to sleep, but still not working correctly on S3. Changed version number for consistency.
    [MagicImageWand.h]
2024-05-28 Fixed the thumbnail position for the S3 version.
    [MIWconfig.h, MagicImageWand.h]
2024-05-28 Fixed thumbnail size for images not 144 tall.
    [MagicImageWand.h]
2024-05-29 Fixed name filter to ignore extension. #70 Fixed the brightness issues on S3. #72
    [MagicImageWand.h]
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
